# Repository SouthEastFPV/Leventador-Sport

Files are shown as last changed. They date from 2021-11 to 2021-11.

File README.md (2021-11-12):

# Leventador Sport
Open Source FPV Drone Box Racing Frame project initiated by SouthEastFPV - Rick Caudle AKA - SSBelmont
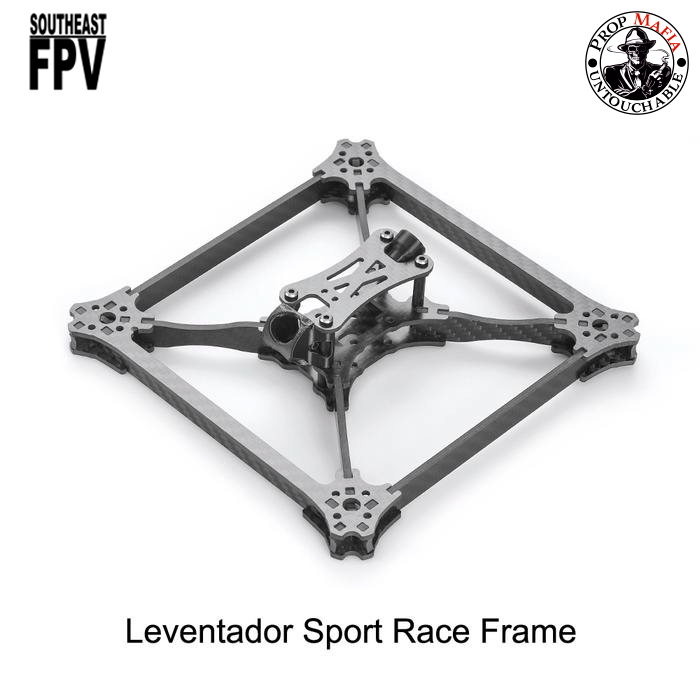
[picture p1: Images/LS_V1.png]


# About Leventador Sport
## The idea
The Leventador Sport is the first super durable Box, open source collaborative race frame project. It empowers the community to integrate best practices and current trends into a continuously manufactured FPV Box Race frame. The durability, documentation and capability of this frame puts it on track to be one of the best Box racing frames for newcomers and professionals alike. This Frame was inspired by the Leventador Pro Race Frame and at the request of Mark Grohe (2DogRC) and Roger Bess who I have been racing with for years. Mark and Roger liked the Leventador Pro (a lighter version) but wanted something super durable.  I created this version specifically for them and it has proven to be insanely durable, more durable than many race frames on the market. It survived 12hrs of Mayhem without one broken carbon fiber part and I am not aware of any frame that has be able to do that. It's not the lightest coming in at 100g, as compared to the 74gr the Pro version, but if you are looking for frame that flies on rails and is near indestructible, this is one for you. 

## Frame specifications
* Wheelbase 5": 197mm
* Top plate: 2mm
* Mid plate: 2.5mm 
* Bottom plate 2.5mm
* Arm: 3mm
* Front Rear Brace: 3mm
* Side Brace: 3mm
* Dual Mount: 2.5mm
* Mount: 2.5mm
* Lipo Pad: 2mm (optional)
* Stack mounting:  20 x 20
* Weight 5": 100g

## Hardware
* 4x M3x10 Knurled Standoffs with or without threads (optional)
* 4x M3x20 Knurled Standoffs 
* 4x M3x18 Button Head Bolts
* 4x M3x8 Button Head Bolts
* 16x M3x14mm Socket Head Bolts (motor mounting)

## Project links
* Project discussion: https://discord.gg/AsXFzmGM 
* Project files: https://github.com/SouthEastFPV/Leventador-Sport 
* 3D-printed accessories: https://www.thingiverse.com/tag:leventador

Please use the tag "leventador" when uploading files to thingiverse.com

## Where to buy
* [www.diatone.us](https://www.diatone.us/collections/leventadorx/products/leventadorx-sport-frame)
* [www.southeastfpv.com](no longer being sold)

## Carbon Fiber sources and CNC Services
More Information here: https://github.com/SouthEastFPV/Leventador-Sport/blob/main/CF_CNCServices.md

## Compatibility

| Part | v1| 
| ---  | ---  |
| top plate |fits both LS LP | 
| bottom plate |fits only v1 LS | 
| mid plate |fits only v1 LS | 
| arms |fits only v1 LS | 
| front rear brace |fits only v1 LS | 
| side brace |fits only v1 LS | 
| dual mount |fits only v1 LS | 
| mount |fits only v1 LS |
| lipo pad |fits both LS LP | 

## Changelog
### Leventador Sport v1
* v1 Design complete/tested/vetted in 2021 MultiGP Season

* initial release from SouthEast FPV

## Project license
The frame files are released under GNU Public License (GPL) V3. More information here: https://www.gnu.org/licenses/gpl-3.0.en.html 

## Project naming requirements
Leventador Sport is the name of the frame.  If you are thinking about manufacturing it, you are expected to prefix the name with a brand name in order to allow customers to distinguish the different manufacturers, e.g. “SOUTHEAST LEVENTADOR SPORT”. As a manufacturer you are also expected to denote the version number of the frame files that you have used as basis of the project, e.g. “SOUTHEAST LEVENTADOR V1”. 
If you have forked the project, you need to give it another name in order to avoid confusion between LEVENTADOR SPORT and your project.
Accessories from the LEVENTADOR SPORT project also need to be named with the entire prefix, e.g. “SOUTHEAST LEVENTADOR FPV Camera Mount”. Unless the file is not compatible with certain versions of the frame, the compatible version number or version range also needs to be included in the name, e.g. “SOUTHEAST LEVENTADOR FPV Camera Mount V1 - V2”

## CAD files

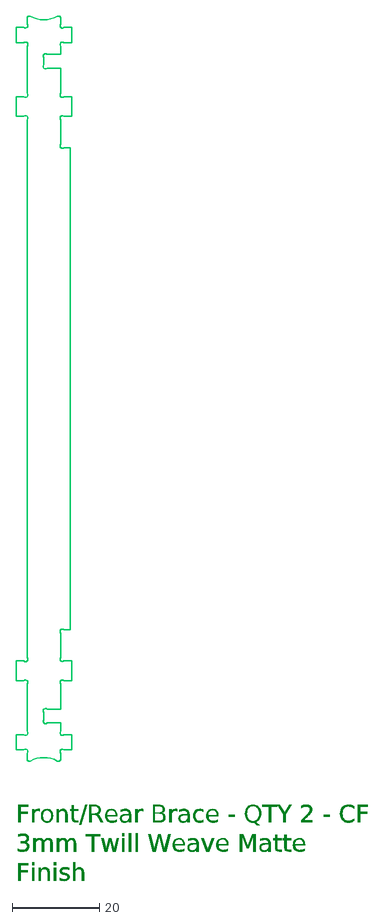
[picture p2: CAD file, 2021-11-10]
LS_Front_Rear_Brace_3mm_2x.dxf
Front/Rear Brace - QTY 2 - CF 3mm Twill Weave Matte Finish

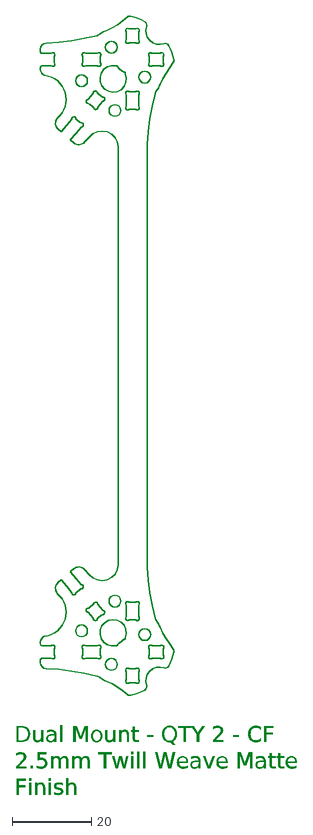
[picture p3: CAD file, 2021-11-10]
LS_Dual_Mount_2.5mm_2x.dxf
Dual Mount - QTY 2 - CF 2.5mm Twill Weave Matte Finish

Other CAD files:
LS_Mount_2.5mm_4x.dxf
L_Top_Plate_2mm.dxf
LS_LipoPad.dxf
LS_MidPlate_2.5mm.dxf
LS_Arm_3mm_4x.dxf
LS_Side_Brace_3mm_2x.dxf
LS_Bottom_Plate_2.5mm.dxf
